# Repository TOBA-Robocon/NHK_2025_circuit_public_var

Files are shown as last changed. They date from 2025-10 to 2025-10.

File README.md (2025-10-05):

# 前提(注意)
USB-CのD+,D-にCANを流す異端ゲキヤバ思想。
USBに規格外信号を流すなって人はブラウザバックを推奨。
著作権保護とかのために本番で使ったデータをちょっと改変してたりする。

# 各基板説明

## CAN_HUB_SMD
USB-CのCANバスを分岐するための基板。

付属のXT60に給電することで分岐先のUSB-Cの電源ラインに電源を供給できる。

電源を供給することで後述する「偽C610(C810)」を駆動させることができる。

本番で使った基板にはれな子のシルクが乗っているため、部内では「れな子」と呼ばれていた。

## CANはぶ
CAN_HUB_SMDの旧バージョン。

使ってるUSB-Cのコネクタが違う。

## GOD_DC_MD
強いモタドラ

定格:40V/60A

## Next_main_Control
メインの基板。

ESP32とF405RGTがついている。Dualshock4の値をESP32で受け取ってCANバスに流し散らかす。

Dualshock4の値を使って各機構の処理をし、4本のUSB-C_CANで各基板にデータを転送する。

ESP32で流すデータの種類とか規格は「ESP32」フォルダの中を参照のこと。

## mecanum_HUB
メカナムを動かしている基板

CAN*1、ロリコン*2(XAコネクタ5pin)、リミットスイッチ*2(XAコネクタ2pin)、電流センサ*2、「GOD_DC_MD」を刺すスロット*2,

メイン基板からのデューティー比と回転方向司令をCANで受けてメカナムを回す

## ガチ夫
ベル直道機構をPID制御する基板

定格:40V/20A

CAN*1、ロリコン*1(XAコネクタ5pin)、リミットスイッチ*1(PHコネクタ2pin)、電流センサ*1、モータードライバ*1ch

メイン基板から速度司令をCANで受けて定速度でベル直を回す。

## 偽C610(C810)
C610サイズのDCモータードライバ

定格:24V/5A

USB-Cから電源とCANを引ける

CAN*1、リミットスイッチ*1(PHコネクタ2pin)、モータードライバ*1ch

メイン基板からデューティー比と回転方向司令をCANで受けてモーターを回す。

基板をロボットに固定するのがめんどくさすぎる駄作。

# iocs
各基板に乗っているSTM32用の.iocファイル群

参考程度にCubeIDE等で使って、どうぞ。

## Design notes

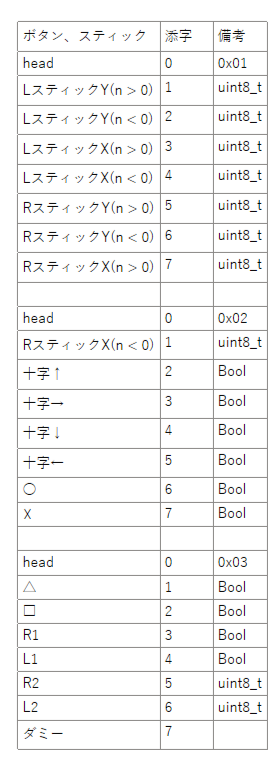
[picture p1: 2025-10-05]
ESP32/スクリーンショット 2025-10-06 024648.png

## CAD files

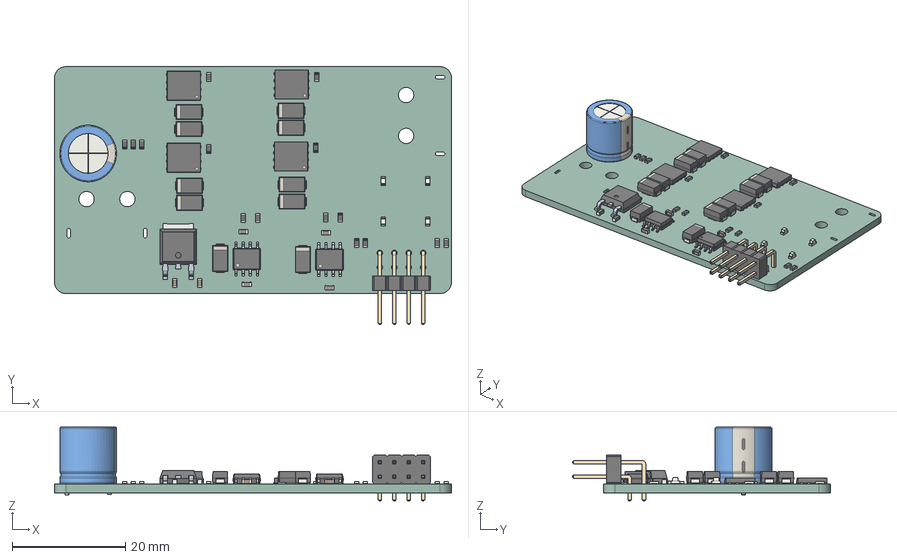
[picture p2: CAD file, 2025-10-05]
GOD_DC_MD/GOD_DC_MD.step
70.0 x 45.4 x 13.0 mm
CP_Radial_D100mm_P750mm
D_SMA x 10
SOIC_8_39x49mm_P127mm x 2
PinHeader_2x04_P254mm_Horizontal
C_0603_1608Metric x 6
R_0603_1608Metric x 15
TDSON_8_1 x 4
LED_0603_1608Metric x 4
CQ assembly
GOD_DC_MD_PCB

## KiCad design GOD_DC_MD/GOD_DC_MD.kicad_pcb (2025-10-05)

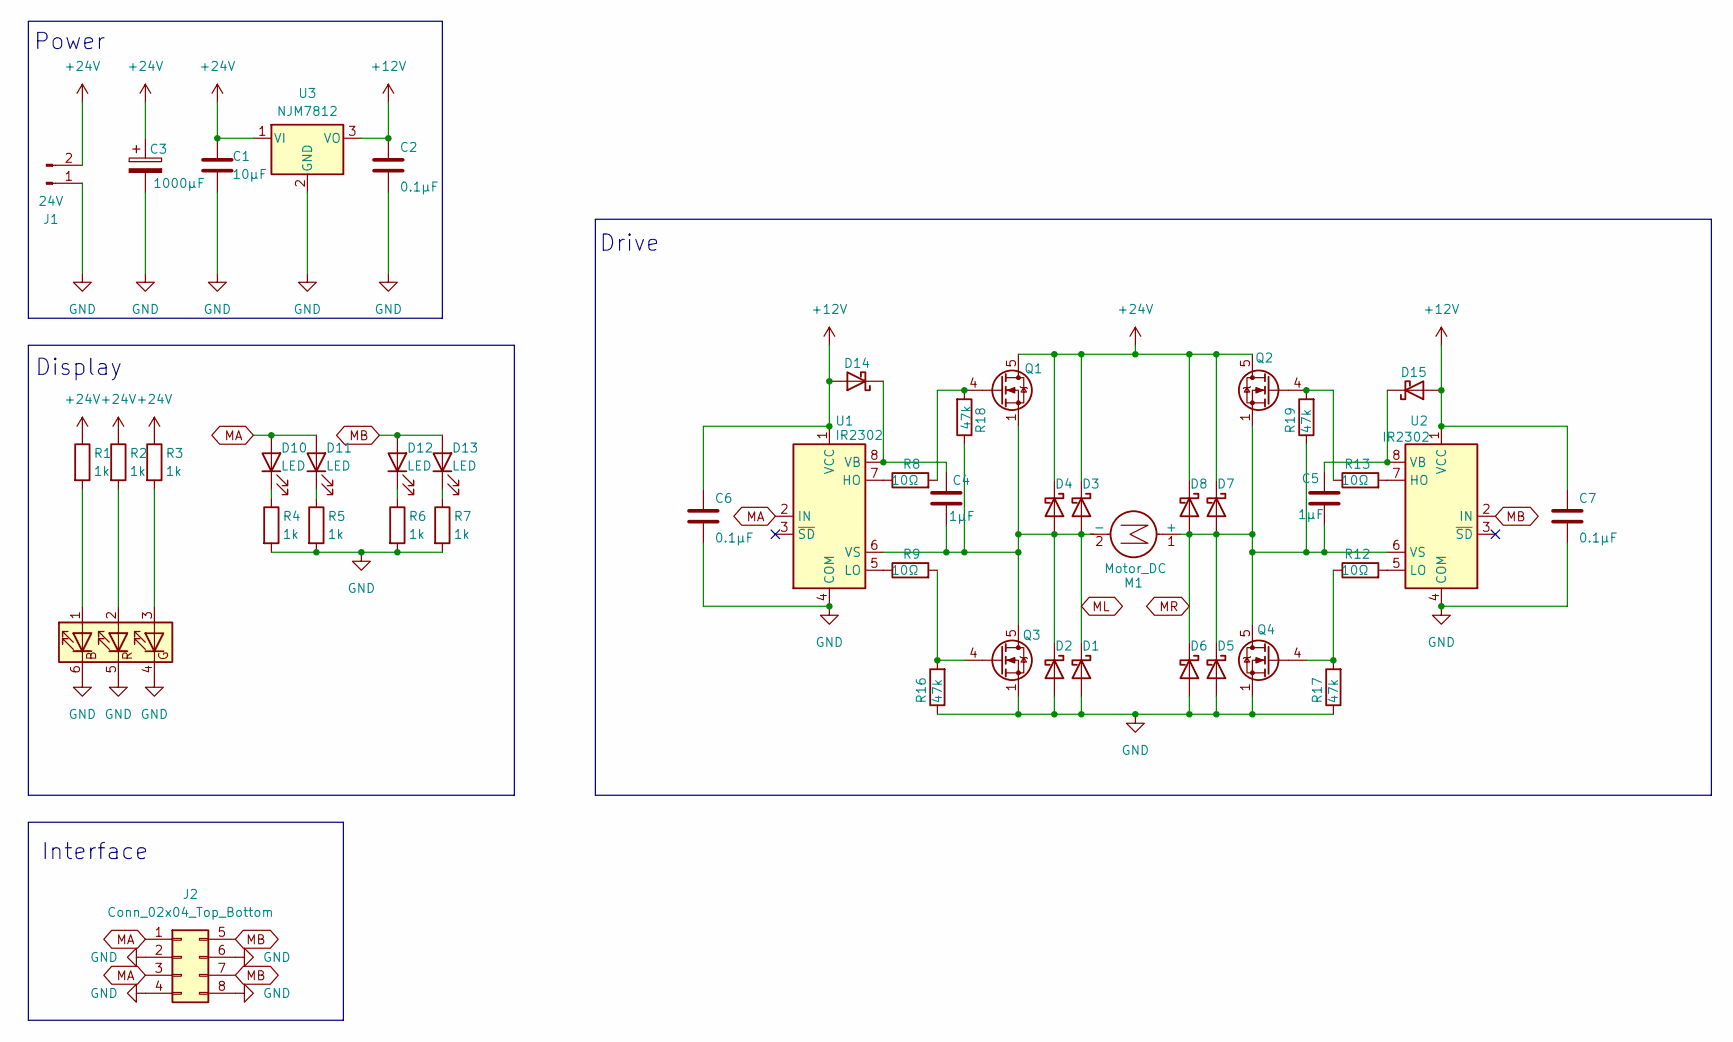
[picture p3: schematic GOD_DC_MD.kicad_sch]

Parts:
C1: 10μF; C_0603_1608Metric_Pad1.08x0.95mm_HandSolder
C2, C6, C7: 0.1μF; C_0603_1608Metric_Pad1.08x0.95mm_HandSolder
C3: 1000μF; CP_Radial_D10.0mm_P7.50mm
C4, C5: 1μF; C_0603_1608Metric_Pad1.08x0.95mm_HandSolder
D1, D2, D3, D4, D5, D6, D7, D8, D14, D15: SS14; D_SMA_Handsoldering
D9: SMLVN6RGB; LED_ROHM_SMLVN6
D10, D11, D12, D13: LED; LED_0603_1608Metric_Pad1.05x0.95mm_HandSolder
J1: 24V; AMASS_XT60PW-M_1x02_P7.20mm_Horizontal
J2: Conn_02x04_Top_Bottom; PinHeader_2x04_P2.54mm_Horizontal
M1: Motor_DC; AMASS_XT60PW-F_1x02_P7.20mm_Horizontal
Q1, Q2, Q3, Q4: BSC159N10LSFG; TDSON-8-1
R1, R2, R3, R4, R5, R6, R7: 1k; R_0603_1608Metric_Pad0.98x0.95mm_HandSolder
R8, R9, R12, R13: 10Ω; R_0603_1608Metric_Pad0.98x0.95mm_HandSolder
R16, R17, R18, R19: 47k; R_0603_1608Metric_Pad0.98x0.95mm_HandSolder
U1, U2: IR2302; SOIC-8_3.9x4.9mm_P1.27mm
U3: NJM7812; TO-252-2

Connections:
+12V: C2.1, C6.1, C7.1, D14.2 (A), D15.2 (A), U1.1 (VCC), U2.1 (VCC), U3.3 (VO)
+24V: C1.1, C3.1, D3.1 (K), D4.1 (K), D7.1 (K), D8.1 (K), J1.2, Q1.5 (D), Q2.5 (D), R1.1, R2.1, R3.1, U3.1 (VI)
GND: C1.2, C2.2, C3.2, C6.2, C7.2, D1.2 (A), D2.2 (A), D5.2 (A), D6.2 (A), D9.4 (GK), D9.5 (RK), D9.6 (BK), J1.1, J2.2, J2.4, J2.6, J2.8, Q3.1 (S), Q3.2 (S), Q3.3 (S), Q4.1 (S), Q4.2 (S), Q4.3 (S), R4.2, R5.2, R6.2, R7.2, R16.1, R17.1, U1.4 (COM), U2.4 (COM), U3.2 (GND)
MA: D10.2 (A), D11.2 (A), J2.1, J2.3, U1.2 (IN)
MB: D12.2 (A), D13.2 (A), J2.5, J2.7, U2.2 (IN)
ML: C4.2, D1.1 (K), D2.1 (K), D3.2 (A), D4.2 (A), M1.2 (-), Q1.1 (S), Q1.2 (S), Q1.3 (S), Q3.5 (D), R18.1, U1.6 (VS)
MR: C5.2, D5.1 (K), D6.1 (K), D7.2 (A), D8.2 (A), M1.1 (+), Q2.1 (S), Q2.2 (S), Q2.3 (S), Q4.5 (D), R19.1, U2.6 (VS)
unnamed: D9.1 (BA), R1.2
unnamed: D9.3 (GA), R3.2
unnamed: D9.2 (RA), R2.2
unnamed: D10.1 (K), R4.1
unnamed: D11.1 (K), R5.1
unnamed: D12.1 (K), R6.1
unnamed: D13.1 (K), R7.1
unnamed: C4.1, D14.1 (K), U1.8 (VB)
unnamed: C5.1, D15.1 (K), U2.8 (VB)
unnamed: Q1.4 (G), R8.2, R18.2
unnamed: Q2.4 (G), R13.1, R19.2
unnamed: Q3.4 (G), R9.2, R16.2
unnamed: Q4.4 (G), R12.1, R17.2
unnamed: R8.1, U1.7 (HO)
unnamed: R9.1, U1.5 (LO)
unnamed: R13.2, U2.7 (HO)
unnamed: R12.2, U2.5 (LO)

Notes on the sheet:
Display
Drive
Interface
Power

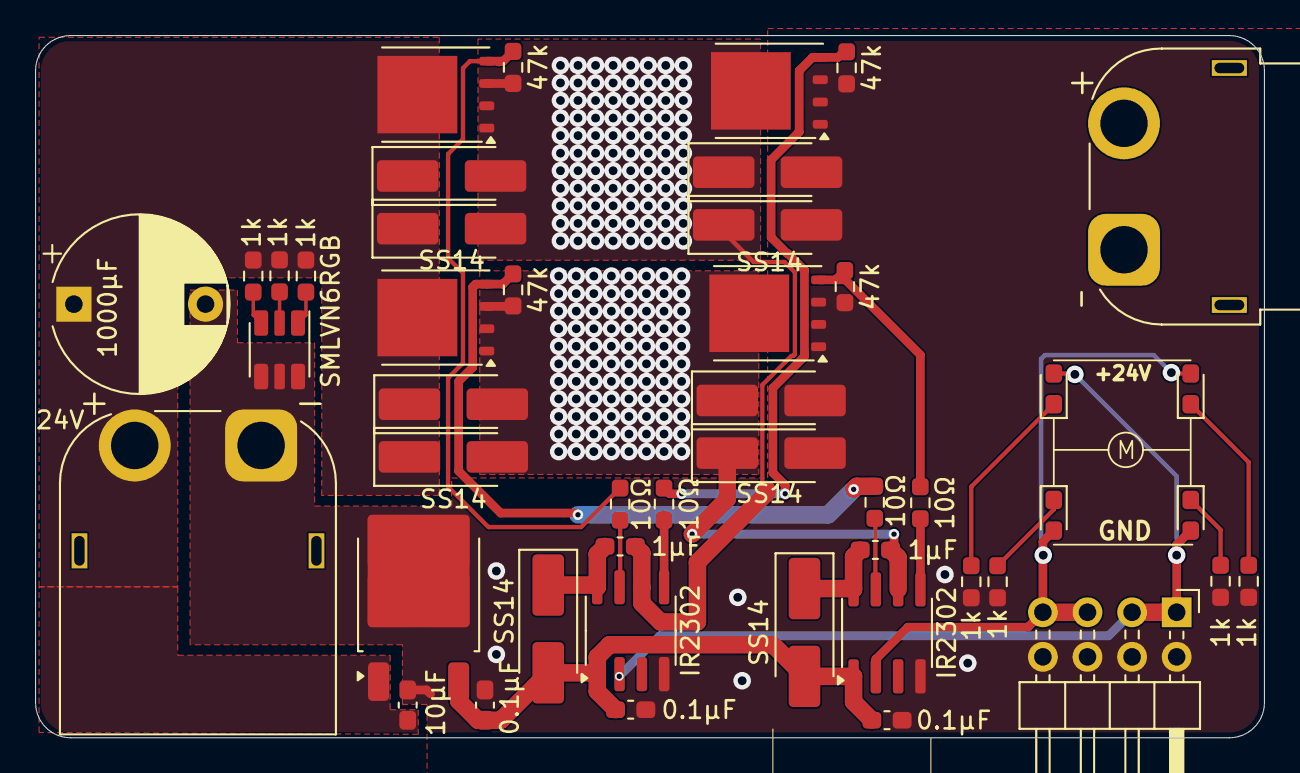
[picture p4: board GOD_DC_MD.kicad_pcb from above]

Board: 2 copper layers, 70.0 x 40.0 mm, 47 parts (0 on the bottom side), 24 nets.

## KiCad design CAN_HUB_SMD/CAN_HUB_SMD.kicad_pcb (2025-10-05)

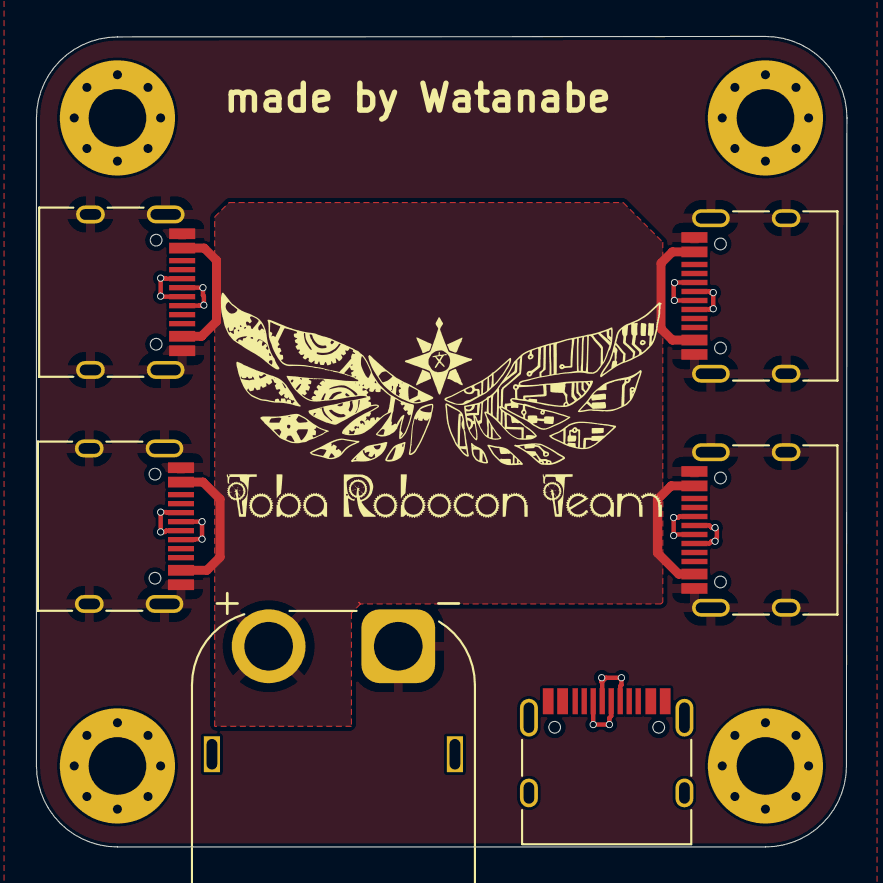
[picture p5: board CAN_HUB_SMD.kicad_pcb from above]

Board: 2 copper layers, 45.0 x 45.0 mm, 10 parts (0 on the bottom side), 5 nets.

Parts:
H1, H2, H3, H4: MountingHole_Pad; MountingHole_3.2mm_M3_Pad_Via
J1: Conn_01x02_Pin; AMASS_XT60PW-M_1x02_P7.20mm_Horizontal
J2, J3, J4, J5, J6: USB_C_Receptacle_USB2.0_16P; USB_C_Receptacle_HRO_TYPE-C-31-M-12

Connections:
+24V: J1.2, J3.A4 (VBUS), J3.A9 (VBUS), J3.B4 (VBUS), J3.B9 (VBUS), J4.A4 (VBUS), J4.A9 (VBUS), J4.B4 (VBUS), J4.B9 (VBUS), J5.A4 (VBUS), J5.A9 (VBUS), J5.B4 (VBUS), J5.B9 (VBUS), J6.A4 (VBUS), J6.A9 (VBUS), J6.B4 (VBUS), J6.B9 (VBUS)
CAN_H: J2.A6 (D+), J2.B6 (D+), J3.A6 (D+), J3.B6 (D+), J4.A6 (D+), J4.B6 (D+), J5.A6 (D+), J5.B6 (D+), J6.A6 (D+), J6.B6 (D+)
CAN_L: J2.A7 (D-), J2.B7 (D-), J3.A7 (D-), J3.B7 (D-), J4.A7 (D-), J4.B7 (D-), J5.A7 (D-), J5.B7 (D-), J6.A7 (D-), J6.B7 (D-)
GND: J1.1, J3.A1 (GND), J3.A12 (GND), J3.B1 (GND), J3.B12 (GND), J3.S1 (SHIELD), J4.A1 (GND), J4.A12 (GND), J4.B1 (GND), J4.B12 (GND), J4.S1 (SHIELD), J5.A1 (GND), J5.A12 (GND), J5.B1 (GND), J5.B12 (GND), J5.S1 (SHIELD), J6.A1 (GND), J6.A12 (GND), J6.B1 (GND), J6.B12 (GND), J6.S1 (SHIELD)
unnamed: J2.A1 (GND), J2.A12 (GND), J2.B1 (GND), J2.B12 (GND)

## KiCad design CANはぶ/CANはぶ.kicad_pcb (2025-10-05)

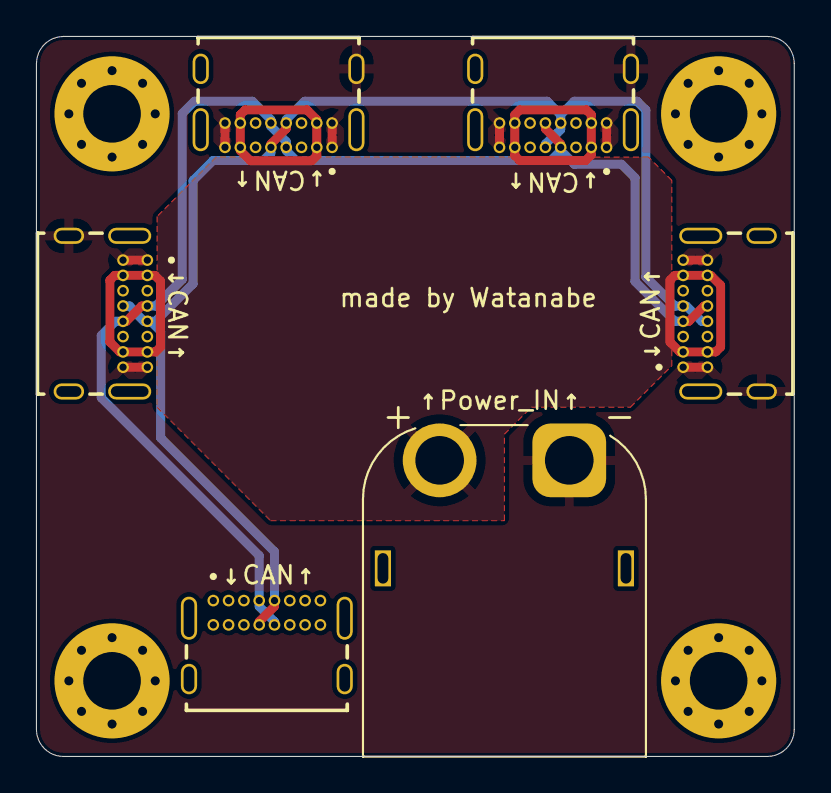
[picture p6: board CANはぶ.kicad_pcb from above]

Board: 2 copper layers, 42.1 x 40.0 mm, 10 parts (0 on the bottom side), 4 nets.

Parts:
H1, H2, H3, H4: MountingHole_Pad; MountingHole_3.2mm_M3_Pad_Via
J1, J2, J3, J4, J5: USB_C_Receptacle_USB2.0_16P; GCT_USB4085-GF-A_REVB
J6: Conn_01x02_Pin; AMASS_XT60PW-M_1x02_P7.20mm_Horizontal

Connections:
+24V: J1.A4 (VBUS), J1.A9 (VBUS), J1.B4 (VBUS), J1.B9 (VBUS), J2.A4 (VBUS), J2.A9 (VBUS), J2.B4 (VBUS), J2.B9 (VBUS), J3.A4 (VBUS), J3.A9 (VBUS), J3.B4 (VBUS), J3.B9 (VBUS), J4.A4 (VBUS), J4.A9 (VBUS), J4.B4 (VBUS), J4.B9 (VBUS), J6.2
CAN_H: J1.A7 (D-), J1.B7 (D-), J2.A7 (D-), J2.B7 (D-), J3.A7 (D-), J3.B7 (D-), J4.A7 (D-), J4.B7 (D-), J5.A7 (D-), J5.B7 (D-)
CAN_L: J1.A6 (D+), J1.B6 (D+), J2.A6 (D+), J2.B6 (D+), J3.A6 (D+), J3.B6 (D+), J4.A6 (D+), J4.B6 (D+), J5.A6 (D+), J5.B6 (D+)
GND: J1.A1 (GND), J1.A12 (GND), J1.B1 (GND), J1.B12 (GND), J1.S1 (SHIELD), J2.A1 (GND), J2.A12 (GND), J2.B1 (GND), J2.B12 (GND), J2.S1 (SHIELD), J3.A1 (GND), J3.A12 (GND), J3.B1 (GND), J3.B12 (GND), J3.S1 (SHIELD), J4.A1 (GND), J4.A12 (GND), J4.B1 (GND), J4.B12 (GND), J4.S1 (SHIELD), J6.1

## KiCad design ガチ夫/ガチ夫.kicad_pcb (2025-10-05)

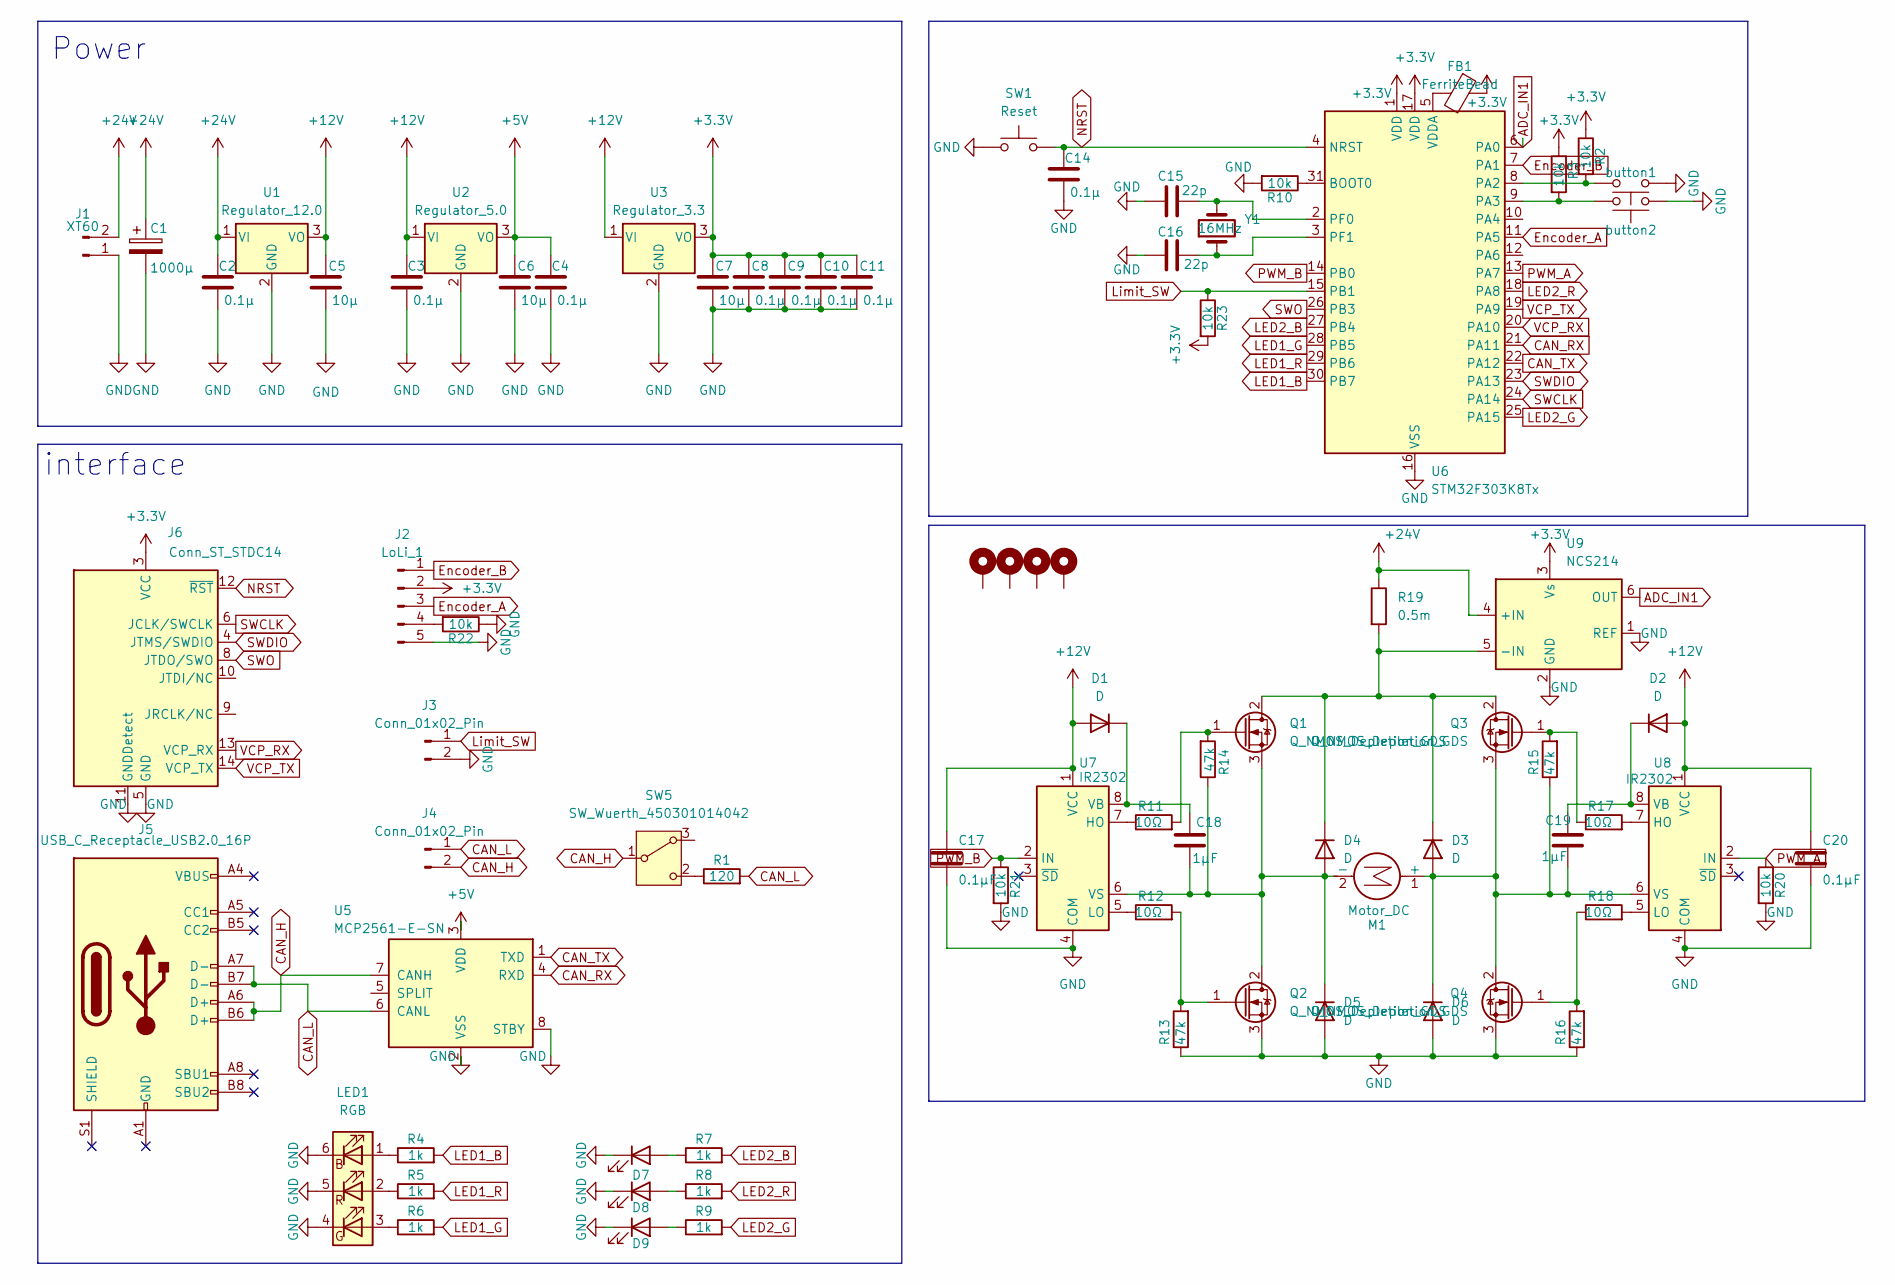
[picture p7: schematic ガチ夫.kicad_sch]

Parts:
C1: 1000μ; CP_Radial_D12.5mm_P5.00mm
C2, C3, C4, C8, C9, C10, C11, C14: 0.1μ; C_0603_1608Metric
C5, C6, C7: 10μ; C_0603_1608Metric
C15, C16: 22p; C_0603_1608Metric
C17, C20: 0.1μF; C_0603_1608Metric_Pad1.08x0.95mm_HandSolder
C18, C19: 1μF; C_0603_1608Metric_Pad1.08x0.95mm_HandSolder
D1, D2, D3, D4, D5, D6: D; D_SOD-123F
D7, D8, D9: LED; LED_0603_1608Metric
FB1: FerriteBead; L_0805_2012Metric_Pad1.05x1.20mm_HandSolder
H1, H2, H3, H4: MountingHole_Pad; MountingHole_3.2mm_M3_Pad_Via
J1: XT60; AMASS_XT60PW-M_1x02_P7.20mm_Horizontal
J2: LoLi_1; JST_XA_B05B-XASK-1_1x05_P2.50mm_Vertical
J3: Conn_01x02_Pin; JST_PH_B2B-PH-SM4-TB_1x02-1MP_P2.00mm_Vertical
J4: Conn_01x02_Pin; JST_XA_S02B-XASK-1N-BN_1x02_P2.50mm_Horizontal
J5: USB_C_Receptacle_USB2.0_16P; GCT_USB4085-GF-A_REVB
J6: Conn_ST_STDC14; PinHeader_2x07_P1.27mm_Vertical
LED1: RGB; LED_ROHM_SMLVN6
M1: Motor_DC; AMASS_XT60PW-F_1x02_P7.20mm_Horizontal
Q1, Q2, Q3, Q4: Q_NMOS_Depletion_GDS; TO-252-2
R1: 120; R_0603_1608Metric_Pad0.98x0.95mm_HandSolder
R2, R3, R10, R20, R21, R22, R23: 10k; R_0603_1608Metric
R4, R5, R6, R7, R8, R9: 1k; R_0603_1608Metric_Pad0.98x0.95mm_HandSolder
R11, R12, R17, R18: 10Ω; R_0603_1608Metric_Pad0.98x0.95mm_HandSolder
R13, R14, R15, R16: 47k; R_0603_1608Metric_Pad0.98x0.95mm_HandSolder
R19: 0.5m; R_2512_6332Metric
SW1: Reset; SW_PUSH_1P1T_6x3.5mm_H5.0_APEM_MJTP1250
SW3: button2; SW_PUSH_1P1T_6x3.5mm_H5.0_APEM_MJTP1250
SW4: button1; SW_PUSH_1P1T_6x3.5mm_H5.0_APEM_MJTP1250
SW5: SW_Wuerth_450301014042; SW_Slide-03_Wuerth-WS-SLTV_10x2.5x6.4_P2.54mm
U1: Regulator_12.0; TO-252-2
U2: Regulator_5.0; TO-252-2
U3: Regulator_3.3; TO-252-2
U5: MCP2561-E-SN; SOIC-8_3.9x4.9mm_P1.27mm
U6: STM32F303K8Tx; LQFP-32_7x7mm_P0.8mm
U7, U8: IR2302; SOIC-8_3.9x4.9mm_P1.27mm
U9: NCS214; SOT-363_SC-70-6_Handsoldering
Y1: 16MHz; Crystal_HC18-U_Vertical

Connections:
+3.3V: C7.1, C8.1, C9.1, C10.1, C11.1, FB1.1, J2.2, J6.3 (VCC), R2.1, R3.1, R23.2, U3.3 (VO), U6.1 (VDD), U6.17 (VDD), U9.3 (Vs)
+5V: C4.1, C6.1, U2.3 (VO), U5.3 (VDD)
+12V: C3.1, C5.1, C17.1, C20.1, D1.2 (A), D2.2 (A), U1.3 (VO), U2.1 (VI), U3.1 (VI), U7.1 (VCC), U8.1 (VCC)
+24V: C1.1, C2.1, J1.2, R19.1, U1.1 (VI), U9.4 (+IN)
ADC_IN1: U6.6 (PA0), U9.6 (OUT)
CAN_H: J4.2, J5.A6 (D+), J5.B6 (D+), SW5.1 (B), U5.7 (CANH)
CAN_L: J4.1, J5.A7 (D-), J5.B7 (D-), R1.2, U5.6 (CANL)
CAN_RX: U5.4 (RXD), U6.21 (PA11)
CAN_TX: U5.1 (TXD), U6.22 (PA12)
Encoder_A: J2.3, U6.11 (PA5)
Encoder_B: J2.1, U6.7 (PA1)
GND: C1.2, C2.2, C3.2, C4.2, C5.2, C6.2, C7.2, C8.2, C9.2, C10.2, C11.2, C14.2, C15.1, C16.1, C17.2, C20.2, D5.2 (A), D6.2 (A), D7.1 (K), D8.1 (K), D9.1 (K), J1.1, J2.5, J3.2, J6.5 (GND), J6.7 (GND), J6.11 (GNDDetect), LED1.4 (GK), LED1.5 (RK), LED1.6 (BK), Q2.3 (S), Q4.3 (S), R10.2, R13.1, R16.1, R20.2, R21.2, R22.1, SW1.1, SW3.1, SW4.1, U1.2 (GND), U2.2 (GND), U3.2 (GND), U5.2 (VSS), U5.8 (STBY), U6.16 (VSS), U6.32 (VSS), U7.4 (COM), U8.4 (COM), U9.1 (REF), U9.2 (GND)
LED1_B: R4.2, U6.30 (PB7)
LED1_G: R6.2, U6.28 (PB5)
LED1_R: R5.2, U6.29 (PB6)
LED2_B: R7.2, U6.27 (PB4)
LED2_G: R9.2, U6.25 (PA15)
LED2_R: R8.2, U6.18 (PA8)
Limit_SW: J3.1, R23.1, U6.15 (PB1)
NRST: C14.1, J6.12 (~RST), SW1.2, U6.4 (NRST)
unnamed: C18.1, D1.1 (K), U7.8 (VB)
unnamed: C19.1, D2.1 (K), U8.8 (VB)
unnamed: C19.2, D3.2 (A), D6.1 (K), M1.1 (+), Q3.3 (S), Q4.2 (D), R15.1, U8.6 (VS)
unnamed: D3.1 (K), D4.1 (K), Q1.2 (D), Q3.2 (D), R19.2, U9.5 (-IN)
unnamed: C18.2, D4.2 (A), D5.1 (K), M1.2 (-), Q1.3 (S), Q2.2 (D), R14.1, U7.6 (VS)
unnamed: D7.2 (A), R7.1
unnamed: D8.2 (A), R8.1
unnamed: D9.2 (A), R9.1
unnamed: J2.4, R22.2
unnamed: LED1.1 (BA), R4.1
unnamed: LED1.3 (GA), R6.1
unnamed: LED1.2 (RA), R5.1
unnamed: Q1.1 (G), R11.2, R14.2
unnamed: Q2.1 (G), R12.2, R13.2
unnamed: Q3.1 (G), R15.2, R17.1
unnamed: Q4.1 (G), R16.2, R18.1
unnamed: R1.1, SW5.2 (C)
unnamed: R10.1, U6.31 (BOOT0)
unnamed: R2.2, SW4.2, U6.8 (PA2)
unnamed: R3.2, SW3.2, U6.9 (PA3)
unnamed: C15.2, U6.2 (PF0), Y1.2
unnamed: C16.2, U6.3 (PF1), Y1.1
unnamed: FB1.2, U6.5 (VDDA)
unnamed: R11.1, U7.7 (HO)
unnamed: R12.1, U7.5 (LO)
unnamed: R17.2, U8.7 (HO)
unnamed: R18.2, U8.5 (LO)
PWM_A: R20.1, U6.13 (PA7), U8.2 (IN)
PWM_B: R21.1, U6.14 (PB0), U7.2 (IN)
SWCLK: J6.6 (JCLK/SWCLK), U6.24 (PA14)
SWDIO: J6.4 (JTMS/SWDIO), U6.23 (PA13)
SWO: J6.8 (JTDO/SWO), U6.26 (PB3)
VCP_RX: J6.13 (VCP_RX), U6.20 (PA10)
VCP_TX: J6.14 (VCP_TX), U6.19 (PA9)

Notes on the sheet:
interface
Power

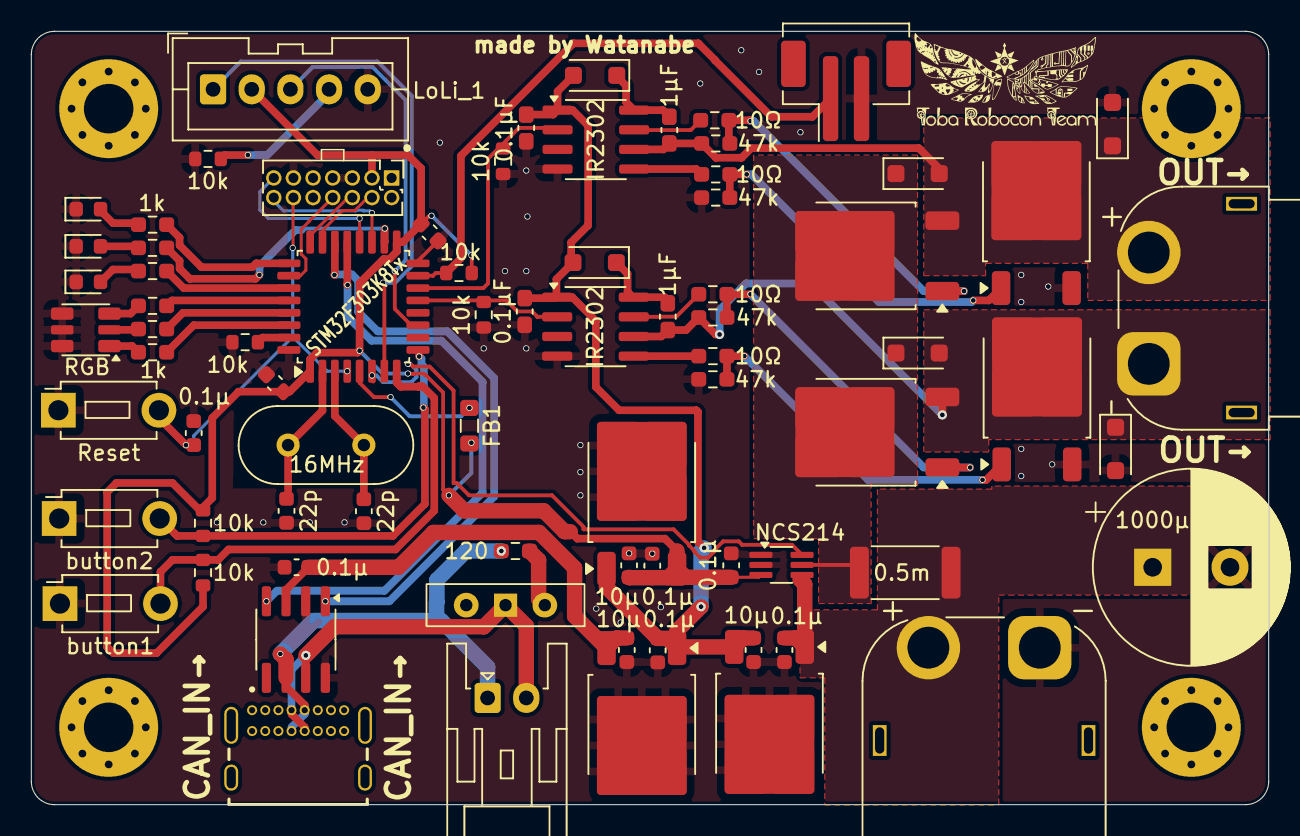
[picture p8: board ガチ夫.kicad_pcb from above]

Board: 2 copper layers, 80.0 x 50.0 mm, 80 parts (0 on the bottom side), 54 nets.

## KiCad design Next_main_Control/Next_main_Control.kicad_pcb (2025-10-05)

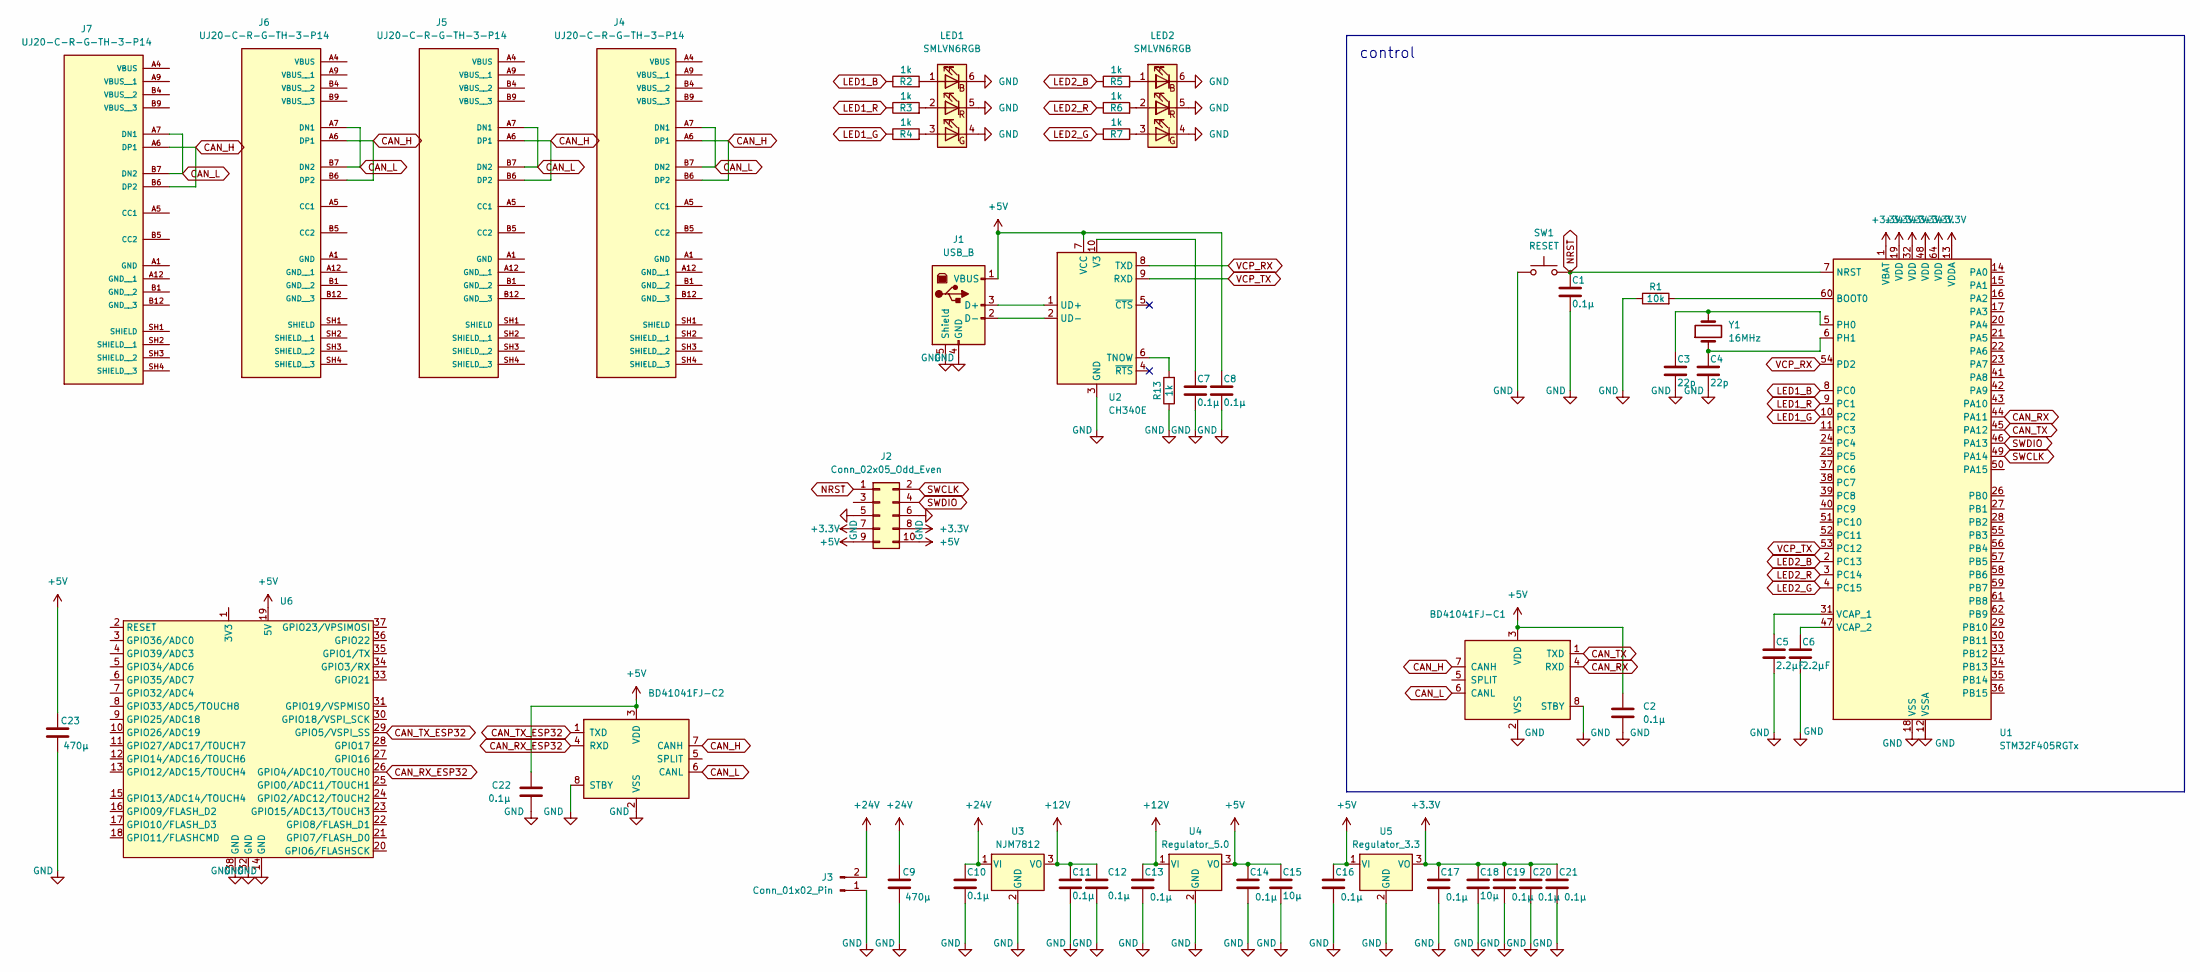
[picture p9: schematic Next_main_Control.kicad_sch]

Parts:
BD41041FJ-C1, BD41041FJ-C2: MCP2561-E-SN; SOIC-8_3.9x4.9mm_P1.27mm
C1, C2, C7, C8, C10, C11, C12, C13, C14, C16, C17, C19, C20, C21, C22: 0.1μ; C_0603_1608Metric_Pad1.08x0.95mm_HandSolder
C3, C4: 22p; C_0603_1608Metric_Pad1.08x0.95mm_HandSolder
C5, C6: 2.2μF; C_0603_1608Metric_Pad1.08x0.95mm_HandSolder
C9, C23: 470μ; CP_Radial_D8.0mm_P5.00mm
C15, C18: 10μ; C_0603_1608Metric_Pad1.08x0.95mm_HandSolder
J1: USB_B; USB_B_OST_USB-B1HSxx_Horizontal
J2: Conn_02x05_Odd_Even; IDC-Header_2x05_P2.54mm_Vertical
J3: Conn_01x02_Pin; AMASS_XT60PW-M_1x02_P7.20mm_Horizontal
J4, J5, J6, J7: UJ20-C-R-G-TH-3-P14; SAMESKY_UJ20-C-R-G-TH-3-P14; PARTREV 1.0
LED1, LED2: SMLVN6RGB; LED_ROHM_SMLVN6
R1: 10k; R_0603_1608Metric_Pad0.98x0.95mm_HandSolder
R2, R3, R4, R5, R6, R7, R13: 1k; R_0603_1608Metric_Pad0.98x0.95mm_HandSolder
SW1: RESET; SW_PUSH_6mm
U1: STM32F405RGTx; LQFP-64_10x10mm_P0.5mm
U2: CH340E; MSOP-10_3x3mm_P0.5mm
U3: NJM7812; TO-252-2
U4: Regulator_5.0; TO-252-2
U5: Regulator_3.3; TO-252-2
U6: ESP32_DevkitC
Y1: 16MHz; Crystal_HC18-U_Vertical

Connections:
+3.3V: C17.1, C18.1, C19.1, C20.1, C21.1, J2.7, J2.8, U1.1 (VBAT), U1.13 (VDDA), U1.19 (VDD), U1.32 (VDD), U1.48 (VDD), U1.64 (VDD), U5.3 (VO)
+5V: BD41041FJ-C1.3 (VDD), BD41041FJ-C2.3 (VDD), C2.1, C8.1, C14.1, C15.1, C16.1, C22.1, C23.1, J1.1 (VBUS), J2.9, J2.10, U2.7 (VCC), U4.3 (VO), U5.1 (VI), U6.19 (5V)
+12V: C11.1, C12.1, C13.1, U3.3 (VO), U4.1 (VI)
+24V: C9.1, C10.1, J3.2, U3.1 (VI)
CAN_H: BD41041FJ-C1.7 (CANH), BD41041FJ-C2.7 (CANH), J4.A6 (DP1), J4.B6 (DP2), J5.A6 (DP1), J5.B6 (DP2), J6.A6 (DP1), J6.B6 (DP2), J7.A6 (DP1), J7.B6 (DP2)
CAN_L: BD41041FJ-C1.6 (CANL), BD41041FJ-C2.6 (CANL), J4.A7 (DN1), J4.B7 (DN2), J5.A7 (DN1), J5.B7 (DN2), J6.A7 (DN1), J6.B7 (DN2), J7.A7 (DN1), J7.B7 (DN2)
CAN_RX: BD41041FJ-C1.4 (RXD), U1.44 (PA11)
CAN_RX_ESP32: BD41041FJ-C2.4 (RXD), U6.26 (GPIO4/ADC10/TOUCH0)
CAN_TX: BD41041FJ-C1.1 (TXD), U1.45 (PA12)
CAN_TX_ESP32: BD41041FJ-C2.1 (TXD), U6.29 (GPIO5/VSPI_SS)
GND: BD41041FJ-C1.2 (VSS), BD41041FJ-C1.8 (STBY), BD41041FJ-C2.2 (VSS), BD41041FJ-C2.8 (STBY), C1.2, C2.2, C3.2, C4.2, C5.2, C6.2, C7.2, C8.2, C9.2, C10.2, C11.2, C12.2, C13.2, C14.2, C15.2, C16.2, C17.2, C18.2, C19.2, C20.2, C21.2, C22.2, C23.2, J1.4 (GND), J1.5 (Shield), J2.5, J2.6, J3.1, LED1.4 (GK), LED1.5 (RK), LED1.6 (BK), LED2.4 (GK), LED2.5 (RK), LED2.6 (BK), R1.1, R13.1, SW1.1, U1.12 (VSSA), U1.18 (VSS), U1.63 (VSS), U2.3 (GND), U3.2 (GND), U4.2 (GND), U5.2 (GND), U6.14 (GND), U6.32 (GND), U6.38 (GND)
LED1_B: R2.1, U1.8 (PC0)
LED1_G: R4.1, U1.10 (PC2)
LED1_R: R3.1, U1.9 (PC1)
LED2_B: R5.1, U1.2 (PC13)
LED2_G: R7.1, U1.4 (PC15)
LED2_R: R6.1, U1.3 (PC14)
NRST: C1.1, J2.1, SW1.2, U1.7 (NRST)
unnamed: J1.3 (D+), U2.1 (UD+)
unnamed: J1.2 (D-), U2.2 (UD-)
unnamed: LED1.1 (BA), R2.2
unnamed: LED1.3 (GA), R4.2
unnamed: LED1.2 (RA), R3.2
unnamed: LED2.1 (BA), R5.2
unnamed: LED2.3 (GA), R7.2
unnamed: LED2.2 (RA), R6.2
unnamed: R1.2, U1.60 (BOOT0)
unnamed: C3.1, U1.5 (PH0), Y1.2
unnamed: C4.1, U1.6 (PH1), Y1.1
unnamed: C5.1, U1.31 (VCAP_1)
unnamed: C6.1, U1.47 (VCAP_2)
unnamed: R13.2, U2.6 (TNOW)
unnamed: C7.1, U2.10 (V3)
SWCLK: J2.2, U1.49 (PA14)
SWDIO: J2.4, U1.46 (PA13)
VCP_RX: U1.54 (PD2), U2.8 (TXD)
VCP_TX: U1.53 (PC12), U2.9 (RXD)

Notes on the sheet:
control

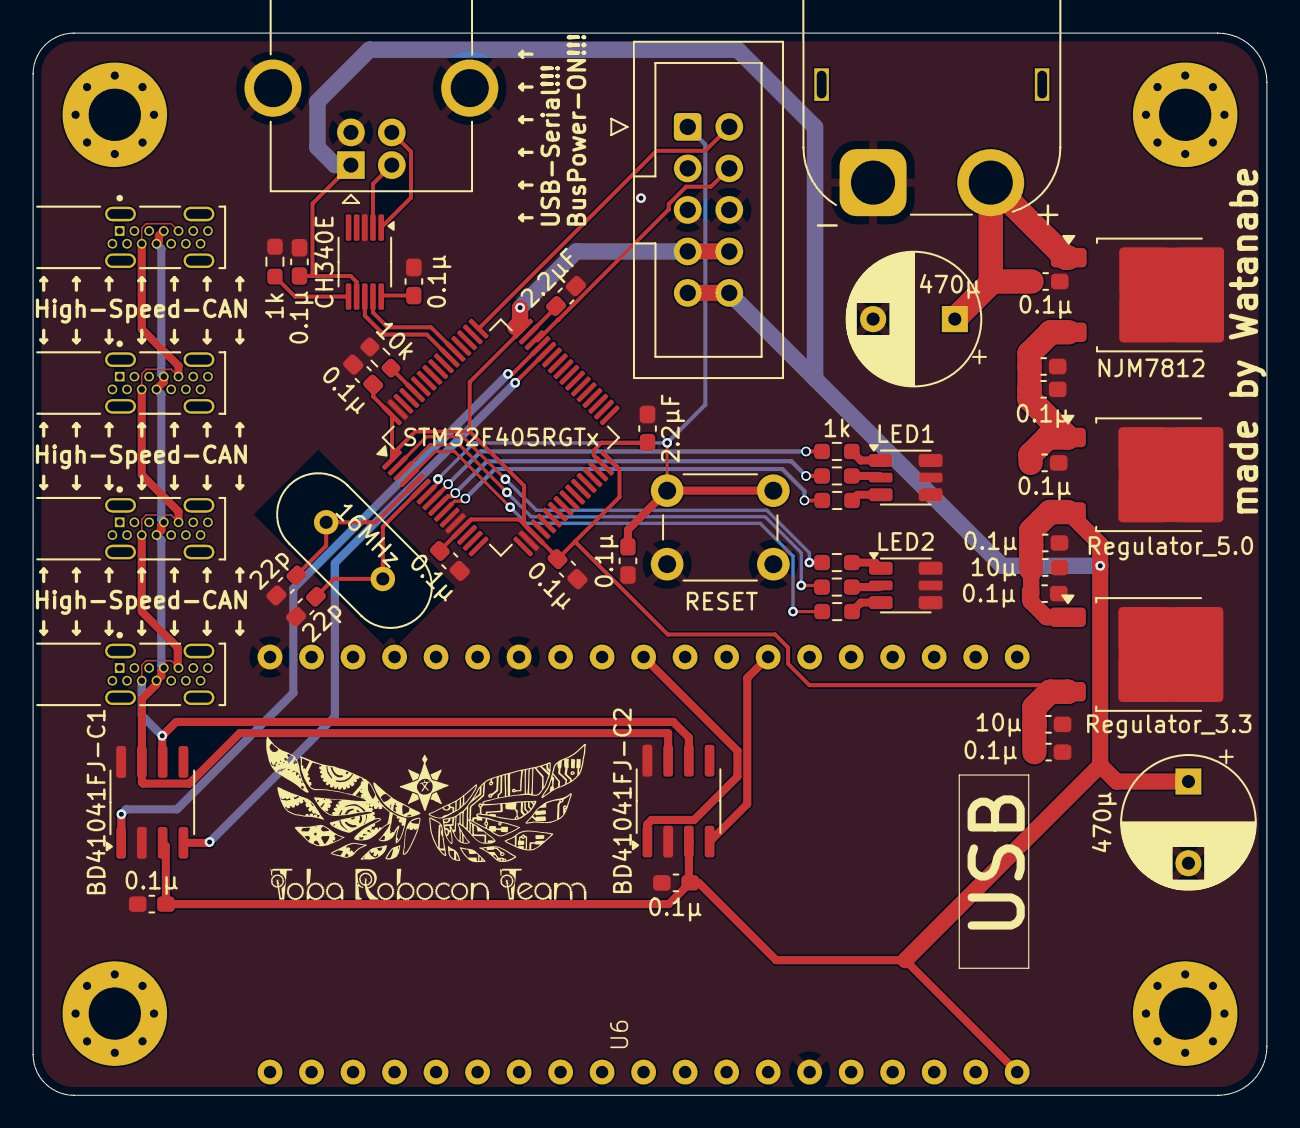
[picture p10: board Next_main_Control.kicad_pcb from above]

Board: 2 copper layers, 75.5 x 65.0 mm, 50 parts (0 on the bottom side), 37 nets.

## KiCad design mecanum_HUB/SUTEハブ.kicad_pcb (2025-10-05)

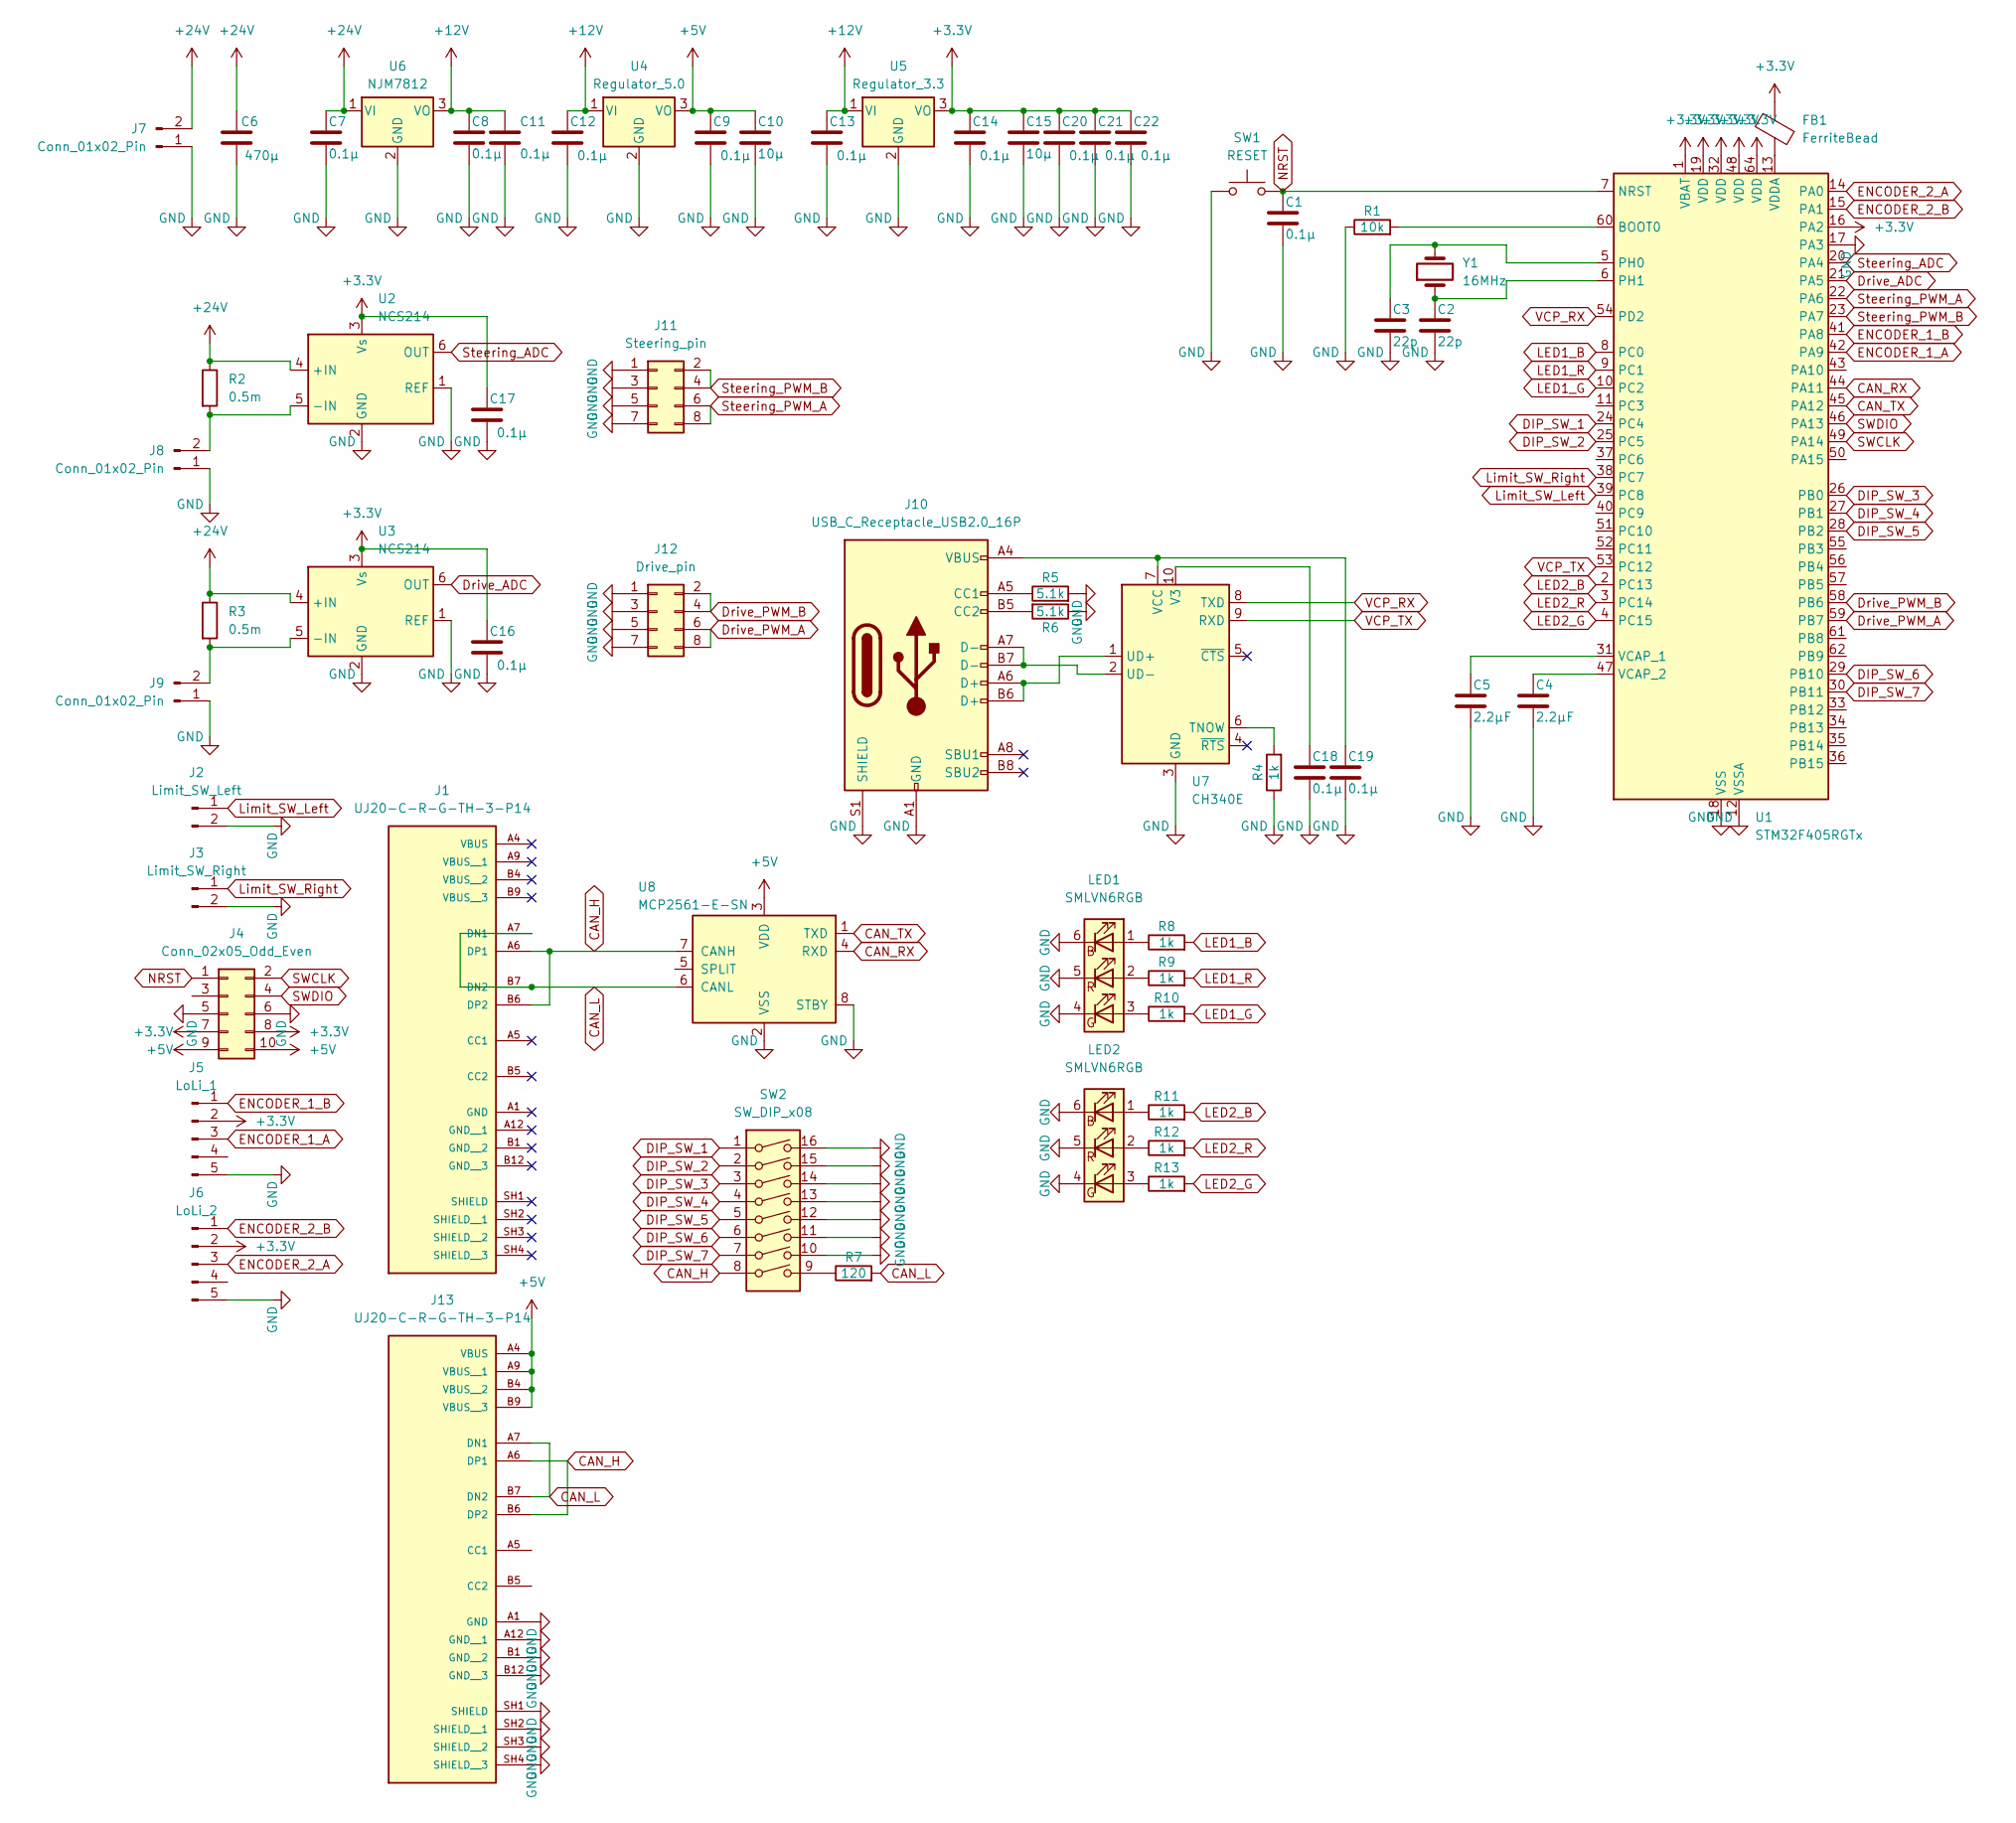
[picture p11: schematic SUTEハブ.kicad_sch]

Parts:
C1, C7, C8, C9, C11, C12, C13, C14, C16, C17, C18, C19, C20, C21, C22: 0.1μ; C_0603_1608Metric_Pad1.08x0.95mm_HandSolder
C2, C3: 22p; C_0603_1608Metric_Pad1.08x0.95mm_HandSolder
C4, C5: 2.2μF; C_0603_1608Metric_Pad1.08x0.95mm_HandSolder
C6: 470μ; CP_Radial_D8.0mm_P5.00mm
C10, C15: 10μ; C_0603_1608Metric_Pad1.08x0.95mm_HandSolder
FB1: FerriteBead; L_0805_2012Metric_Pad1.05x1.20mm_HandSolder
J1, J13: UJ20-C-R-G-TH-3-P14; SAMESKY_UJ20-C-R-G-TH-3-P14; PARTREV 1.0
J2: Limit_SW_Left; JST_XA_B02B-XASK-1_1x02_P2.50mm_Vertical
J3: Limit_SW_Right; JST_XA_B02B-XASK-1_1x02_P2.50mm_Vertical
J4: Conn_02x05_Odd_Even; IDC-Header_2x05_P2.54mm_Vertical
J5: LoLi_1; JST_XA_B05B-XASK-1_1x05_P2.50mm_Vertical
J6: LoLi_2; JST_XA_B05B-XASK-1_1x05_P2.50mm_Vertical
J7: Conn_01x02_Pin; AMASS_XT60PW-M_1x02_P7.20mm_Horizontal
J8, J9: Conn_01x02_Pin; AMASS_XT60-F_1x02_P7.20mm_Vertical
J10: USB_C_Receptacle_USB2.0_16P; USB_C_Receptacle_HRO_TYPE-C-31-M-12
J11: Steering_pin; PinSocket_2x04_P2.54mm_Vertical
J12: Drive_pin; PinSocket_2x04_P2.54mm_Vertical
LED1, LED2: SMLVN6RGB; LED_ROHM_SMLVN6
R1: 10k; R_0603_1608Metric_Pad0.98x0.95mm_HandSolder
R2, R3: 0.5m; R_2512_6332Metric
R4, R8, R9, R10, R11, R12, R13: 1k; R_0603_1608Metric_Pad0.98x0.95mm_HandSolder
R5, R6: 5.1k; R_0603_1608Metric_Pad0.98x0.95mm_HandSolder
R7: 120; R_0603_1608Metric_Pad0.98x0.95mm_HandSolder
SW1: RESET; SW_PUSH_6mm
SW2: SW_DIP_x08; DIP-16_W7.62mm
U1: STM32F405RGTx; LQFP-64_10x10mm_P0.5mm
U2, U3: NCS214; SOT-363_SC-70-6_Handsoldering
U4: Regulator_5.0; TO-252-2
U5: Regulator_3.3; TO-252-2
U6: NJM7812; TO-252-2
U7: CH340E; MSOP-10_3x3mm_P0.5mm
U8: MCP2561-E-SN; SOIC-8_3.9x4.9mm_P1.27mm
Y1: 16MHz; Crystal_HC18-U_Vertical

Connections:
+3.3V: C14.1, C15.1, C16.1, C17.1, C20.1, C21.1, C22.1, FB1.2, J4.7, J4.8, J5.2, J6.2, U1.1 (VBAT), U1.16 (PA2), U1.19 (VDD), U1.32 (VDD), U1.48 (VDD), U1.64 (VDD), U2.3 (Vs), U3.3 (Vs), U5.3 (VO)
+5V: C9.1, C10.1, J4.9, J4.10, J13.A4 (VBUS), J13.A9 (VBUS__1), J13.B4 (VBUS__2), J13.B9 (VBUS__3), U4.3 (VO), U8.3 (VDD)
+12V: C8.1, C11.1, C12.1, C13.1, U4.1 (VI), U5.1 (VI), U6.3 (VO)
+24V: C6.1, C7.1, J7.2, R2.1, R3.1, U2.4 (+IN), U3.4 (+IN), U6.1 (VI)
CAN_H: J1.A6 (DP1), J1.B6 (DP2), J13.A6 (DP1), J13.B6 (DP2), SW2.8, U8.7 (CANH)
CAN_L: J1.A7 (DN1), J1.B7 (DN2), J13.A7 (DN1), J13.B7 (DN2), R7.2, U8.6 (CANL)
CAN_RX: U1.44 (PA11), U8.4 (RXD)
CAN_TX: U1.45 (PA12), U8.1 (TXD)
DIP_SW_1: SW2.1, U1.24 (PC4)
DIP_SW_2: SW2.2, U1.25 (PC5)
DIP_SW_3: SW2.3, U1.26 (PB0)
DIP_SW_4: SW2.4, U1.27 (PB1)
DIP_SW_5: SW2.5, U1.28 (PB2)
DIP_SW_6: SW2.6, U1.29 (PB10)
DIP_SW_7: SW2.7, U1.30 (PB11)
Drive_ADC: U1.21 (PA5), U3.6 (OUT)
Drive_PWM_A: J12.6, J12.8, U1.59 (PB7)
Drive_PWM_B: J12.2, J12.4, U1.58 (PB6)
ENCODER_1_A: J5.3, U1.42 (PA9)
ENCODER_1_B: J5.1, U1.41 (PA8)
ENCODER_2_A: J6.3, U1.14 (PA0)
ENCODER_2_B: J6.1, U1.15 (PA1)
GND: C1.2, C2.2, C3.2, C4.2, C5.2, C6.2, C7.2, C8.2, C9.2, C10.2, C11.2, C12.2, C13.2, C14.2, C15.2, C16.2, C17.2, C18.2, C19.2, C20.2, C21.2, C22.2, J2.2, J3.2, J4.5, J4.6, J5.5, J6.5, J7.1, J8.1, J9.1, J10.A1 (GND), J10.A12 (GND), J10.B1 (GND), J10.B12 (GND), J10.S1 (SHIELD), J11.1, J11.3, J11.5, J11.7, J12.1, J12.3, J12.5, J12.7, J13.A1 (GND), J13.A12 (GND__1), J13.B1 (GND__2), J13.B12 (GND__3), J13.SH1 (SHIELD), J13.SH2 (SHIELD__1), J13.SH3 (SHIELD__2), J13.SH4 (SHIELD__3), LED1.4 (GK), LED1.5 (RK), LED1.6 (BK), LED2.4 (GK), LED2.5 (RK), LED2.6 (BK), R1.1, R4.1, R5.2, R6.1, SW1.1, SW2.10, SW2.11, SW2.12, SW2.13, SW2.14, SW2.15, SW2.16, U1.12 (VSSA), U1.17 (PA3), U1.18 (VSS), U1.63 (VSS), U2.1 (REF), U2.2 (GND), U3.1 (REF), U3.2 (GND), U4.2 (GND), U5.2 (GND), U6.2 (GND), U7.3 (GND), U8.2 (VSS), U8.8 (STBY)
LED1_B: R8.2, U1.8 (PC0)
LED1_G: R10.2, U1.10 (PC2)
LED1_R: R9.2, U1.9 (PC1)
LED2_B: R11.2, U1.2 (PC13)
LED2_G: R13.2, U1.4 (PC15)
LED2_R: R12.2, U1.3 (PC14)
Limit_SW_Left: J2.1, U1.39 (PC8)
Limit_SW_Right: J3.1, U1.38 (PC7)
NRST: C1.1, J4.1, SW1.2, U1.7 (NRST)
unnamed: J8.2, R2.2, U2.5 (-IN)
unnamed: J9.2, R3.2, U3.5 (-IN)
unnamed: J10.A5 (CC1), R5.1
unnamed: J10.B5 (CC2), R6.2
unnamed: LED1.1 (BA), R8.1
unnamed: LED1.3 (GA), R10.1
unnamed: LED1.2 (RA), R9.1
unnamed: LED2.1 (BA), R11.1
unnamed: LED2.3 (GA), R13.1
unnamed: LED2.2 (RA), R12.1
unnamed: R7.1, SW2.9
unnamed: R1.2, U1.60 (BOOT0)
unnamed: C3.1, U1.5 (PH0), Y1.2
unnamed: C2.1, U1.6 (PH1), Y1.1
unnamed: C5.1, U1.31 (VCAP_1)
unnamed: C4.1, U1.47 (VCAP_2)
unnamed: FB1.1, U1.13 (VDDA)
unnamed: R4.2, U7.6 (TNOW)
unnamed: J10.A6 (D+), J10.B6 (D+), U7.1 (UD+)
unnamed: J10.A7 (D-), J10.B7 (D-), U7.2 (UD-)
unnamed: C18.1, U7.10 (V3)
unnamed: C19.1, J10.A4 (VBUS), J10.A9 (VBUS), J10.B4 (VBUS), J10.B9 (VBUS), U7.7 (VCC)
SWCLK: J4.2, U1.49 (PA14)
SWDIO: J4.4, U1.46 (PA13)
Steering_ADC: U1.20 (PA4), U2.6 (OUT)
Steering_PWM_A: J11.6, J11.8, U1.22 (PA6)
Steering_PWM_B: J11.2, J11.4, U1.23 (PA7)
VCP_RX: U1.54 (PD2), U7.8 (TXD)
VCP_TX: U1.53 (PC12), U7.9 (RXD)

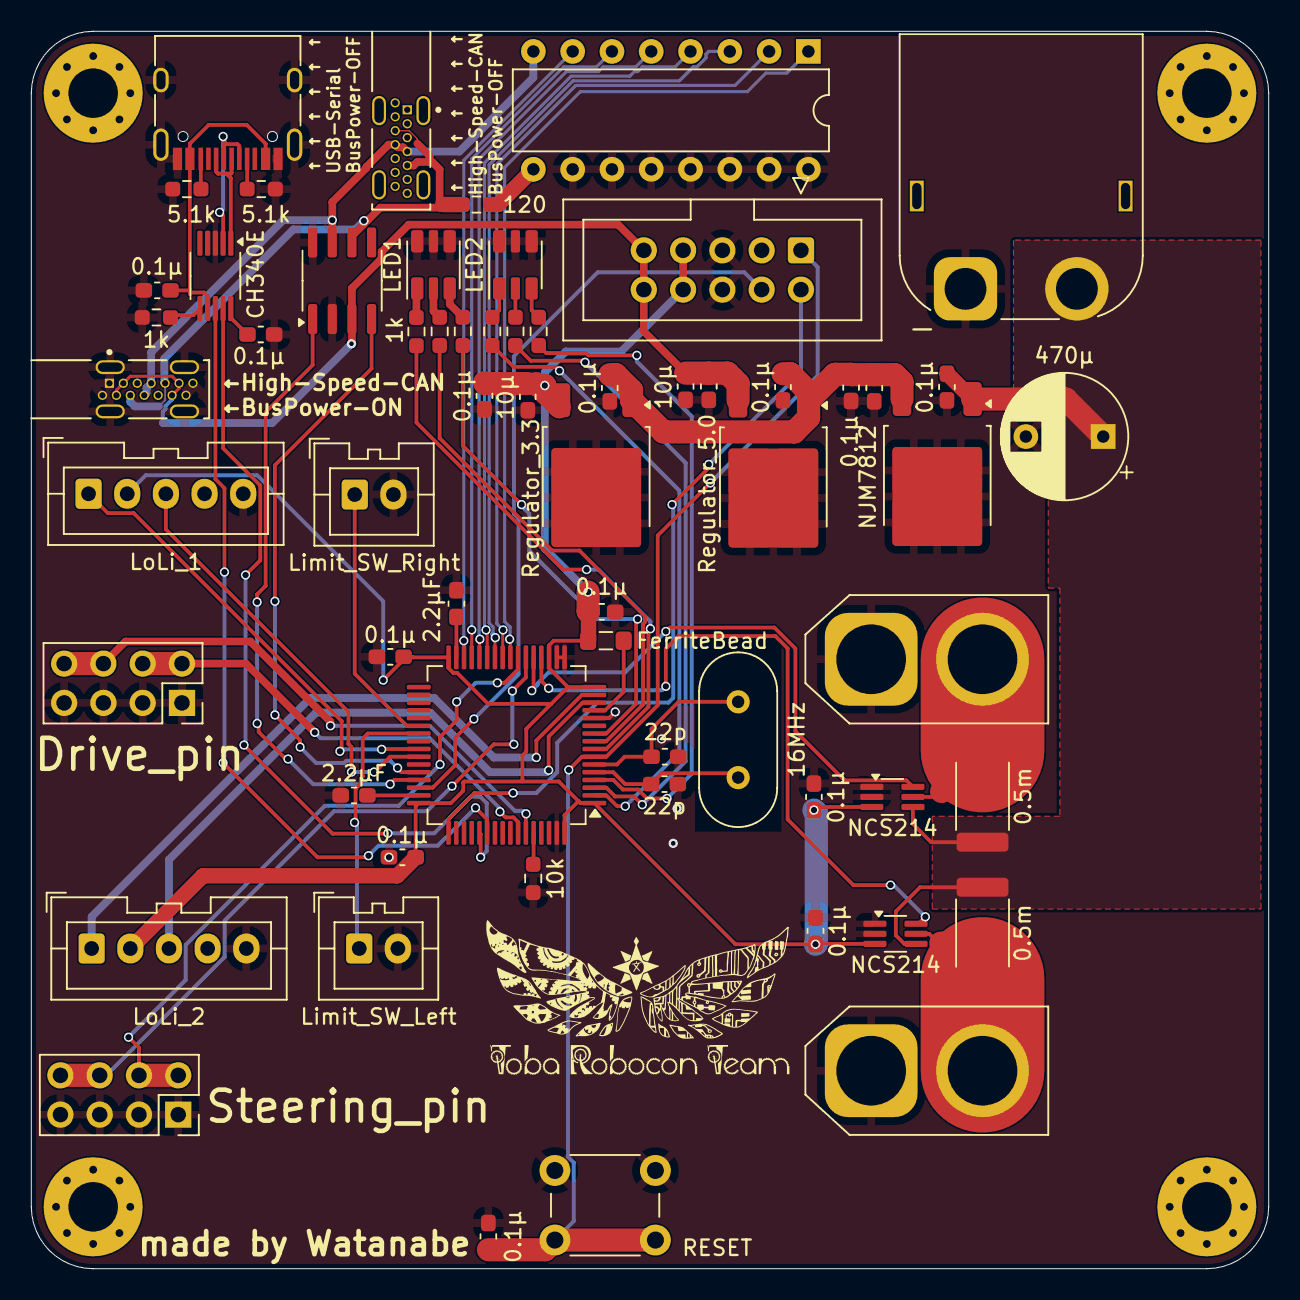
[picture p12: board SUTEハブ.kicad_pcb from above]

Board: 2 copper layers, 80.0 x 80.0 mm, 62 parts (0 on the bottom side), 61 nets.

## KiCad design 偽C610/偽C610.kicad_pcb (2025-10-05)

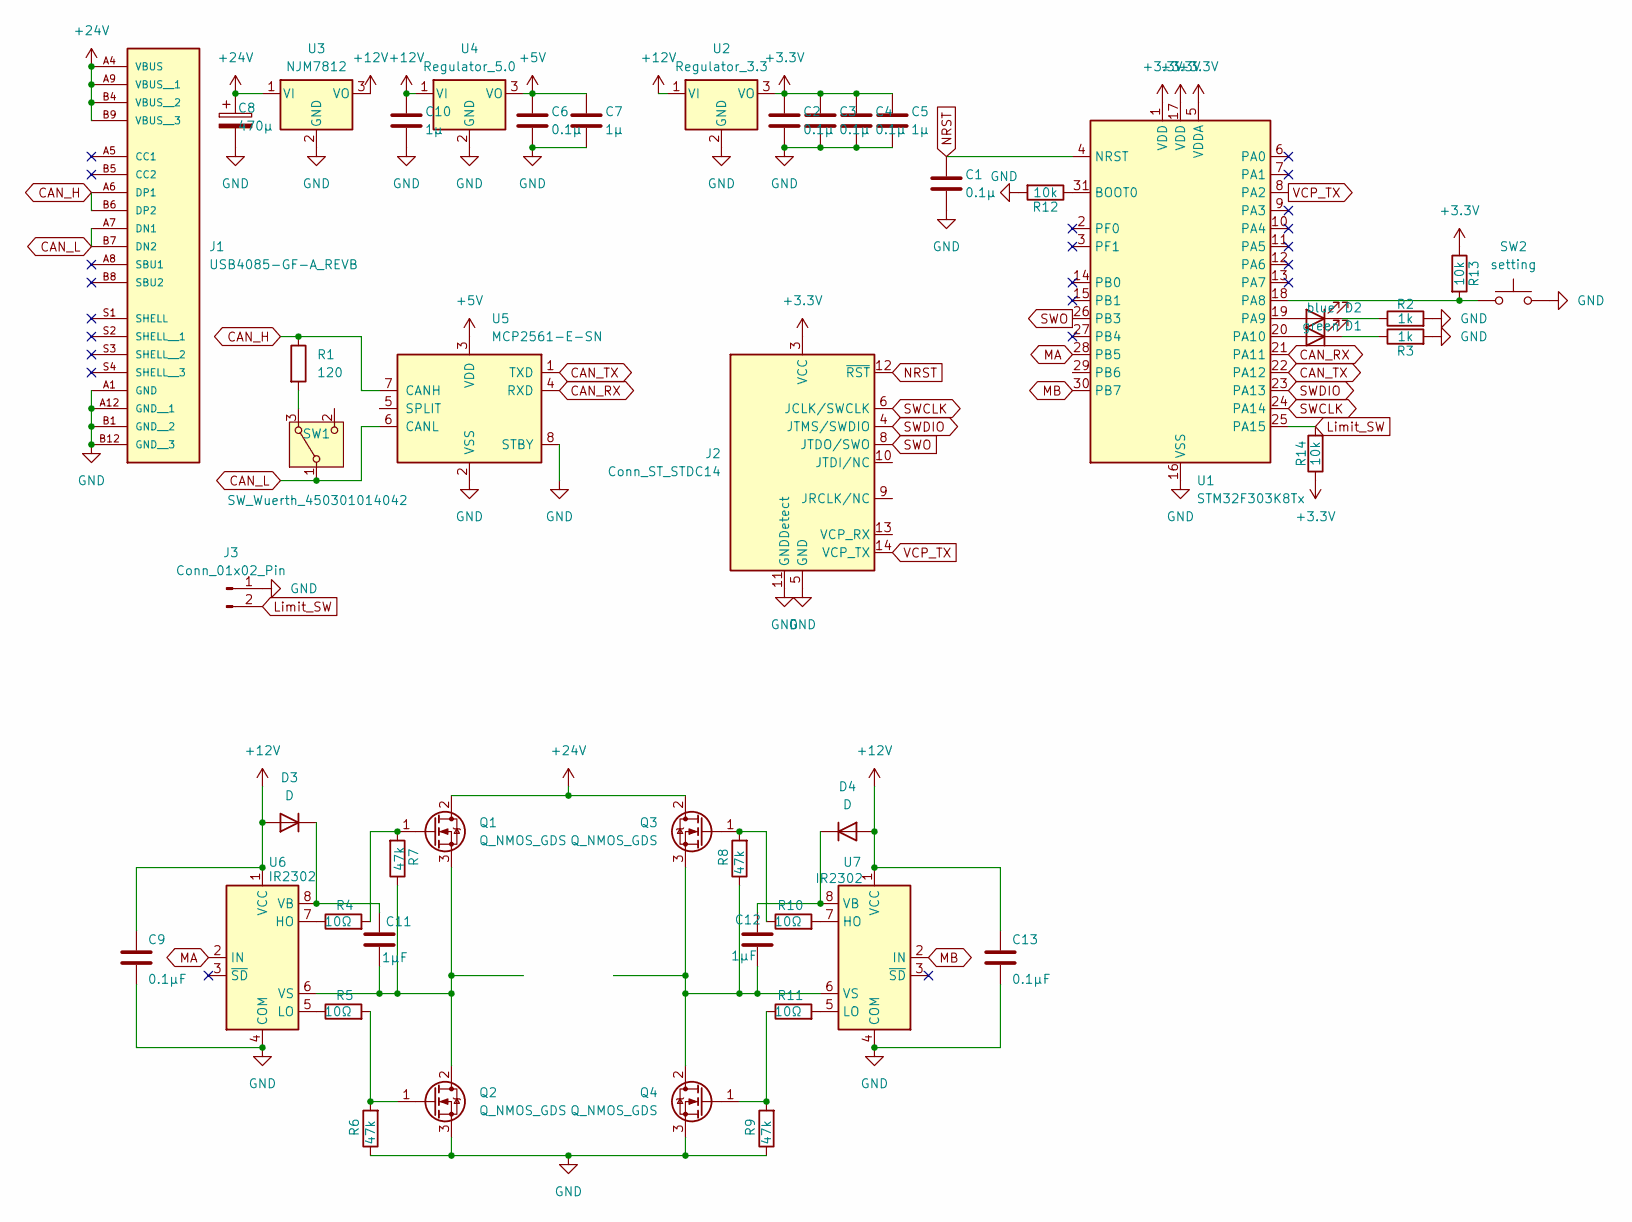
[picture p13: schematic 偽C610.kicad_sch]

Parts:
C1, C2, C3, C4, C6: 0.1μ; C_0603_1608Metric
C5, C7, C10: 1μ; C_0603_1608Metric
C8: 470μ; CP_Radial_D8.0mm_P3.50mm
C9, C13: 0.1μF; C_0603_1608Metric_Pad1.08x0.95mm_HandSolder
C11, C12: 1μF; C_0603_1608Metric_Pad1.08x0.95mm_HandSolder
D1: green; LED_0603_1608Metric
D2: blue; LED_0603_1608Metric
D3, D4: D; D_SOD-123F
J1: USB4085-GF-A_REVB; GCT_USB4085-GF-A_REVB; PARTREV B
J2: Conn_ST_STDC14; PinHeader_2x07_P1.27mm_Vertical
J3: Conn_01x02_Pin; JST_PH_B2B-PH-SM4-TB_1x02-1MP_P2.00mm_Vertical
Q1, Q2, Q3, Q4: Q_NMOS_GDS; TO-252-2
R1: 120; R_0603_1608Metric
R2, R3: 1k; R_0603_1608Metric
R4, R5, R10, R11: 10Ω; R_0603_1608Metric_Pad0.98x0.95mm_HandSolder
R6, R7, R8, R9: 47k; R_0603_1608Metric_Pad0.98x0.95mm_HandSolder
R12, R13, R14: 10k; R_0603_1608Metric
SW1: SW_Wuerth_450301014042; SW_Slide-03_Wuerth-WS-SLTV_10x2.5x6.4_P2.54mm
SW2: setting; SW_PUSH_1P1T_6x3.5mm_H5.0_APEM_MJTP1250
U1: STM32F303K8Tx; LQFP-32_7x7mm_P0.8mm
U2: Regulator_3.3; TO-252-2
U3: NJM7812; TO-252-2
U4: Regulator_5.0; TO-252-2
U5: MCP2561-E-SN; SOIC-8_3.9x4.9mm_P1.27mm
U6, U7: IR2302; SOIC-8_3.9x4.9mm_P1.27mm

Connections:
+3.3V: C2.1, C3.1, C4.1, C5.1, J2.3 (VCC), R13.1, R14.1, U1.1 (VDD), U1.5 (VDDA), U1.17 (VDD), U2.3 (VO)
+5V: C6.1, C7.1, U4.3 (VO), U5.3 (VDD)
+12V: C9.1, C10.1, C13.1, D3.2 (A), D4.2 (A), U2.1 (VI), U3.3 (VO), U4.1 (VI), U6.1 (VCC), U7.1 (VCC)
+24V: C8.1, J1.A4 (VBUS), J1.A9 (VBUS__1), J1.B4 (VBUS__2), J1.B9 (VBUS__3), Q1.2 (D), Q3.2 (D), U3.1 (VI)
CAN_H: J1.A6 (DP1), J1.B6 (DP2), R1.1, U5.7 (CANH)
CAN_L: J1.A7 (DN1), J1.B7 (DN2), SW1.1 (B), U5.6 (CANL)
CAN_RX: U1.21 (PA11), U5.4 (RXD)
CAN_TX: U1.22 (PA12), U5.1 (TXD)
GND: C1.2, C2.2, C3.2, C4.2, C5.2, C6.2, C7.2, C8.2, C9.2, C10.2, C13.2, J1.A1 (GND), J1.A12 (GND__1), J1.B1 (GND__2), J1.B12 (GND__3), J2.5 (GND), J2.7 (GND), J2.11 (GNDDetect), J3.1, Q2.3 (S), Q4.3 (S), R2.2, R3.2, R6.1, R9.1, R12.2, SW2.2, U1.16 (VSS), U1.32 (VSS), U2.2 (GND), U3.2 (GND), U4.2 (GND), U5.2 (VSS), U5.8 (STBY), U6.4 (COM), U7.4 (COM)
Limit_SW: J3.2, R14.2, U1.25 (PA15)
MA: U1.28 (PB5), U6.2 (IN)
MB: U1.30 (PB7), U7.2 (IN)
NRST: C1.1, J2.12 (~RST), U1.4 (NRST)
unnamed: D1.2 (A), U1.20 (PA10)
unnamed: D1.1 (K), R3.1
unnamed: D2.2 (A), U1.19 (PA9)
unnamed: D2.1 (K), R2.1
unnamed: C11.1, D3.1 (K), U6.8 (VB)
unnamed: C12.1, D4.1 (K), U7.8 (VB)
unnamed: Q1.1 (G), R4.2, R7.2
unnamed: C11.2, Q1.3 (S), Q2.2 (D), R7.1, U6.6 (VS)
unnamed: Q2.1 (G), R5.2, R6.2
unnamed: Q3.1 (G), R8.2, R10.1
unnamed: C12.2, Q3.3 (S), Q4.2 (D), R8.1, U7.6 (VS)
unnamed: Q4.1 (G), R9.2, R11.1
unnamed: R1.2, SW1.3 (A)
unnamed: R12.1, U1.31 (BOOT0)
unnamed: R13.2, SW2.1, U1.18 (PA8)
unnamed: R4.1, U6.7 (HO)
unnamed: R5.1, U6.5 (LO)
unnamed: R10.2, U7.7 (HO)
unnamed: R11.2, U7.5 (LO)
SWCLK: J2.6 (JCLK/SWCLK), U1.24 (PA14)
SWDIO: J2.4 (JTMS/SWDIO), U1.23 (PA13)
SWO: J2.8 (JTDO/SWO), U1.26 (PB3)
VCP_TX: J2.14 (VCP_TX), U1.8 (PA2)

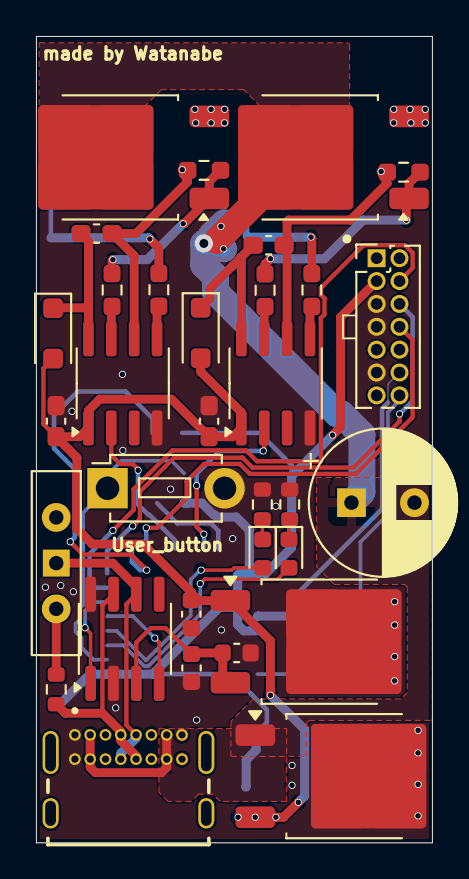
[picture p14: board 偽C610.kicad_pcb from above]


Board: 2 copper layers, 22.0 x 44.8 mm, 47 parts (15 on the bottom side), 36 nets.

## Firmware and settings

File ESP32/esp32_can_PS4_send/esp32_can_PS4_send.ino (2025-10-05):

#include "CAN.h"
#include "PS4Controller.h"

void setup() {
  if(!CAN.begin(1000E3)) //通信速度
  {
    while (1);
    //送信不可
  }
  volatile uint32_t* pREG_IER = (volatile uint32_t*)0x3ff6b010;
  *pREG_IER &= ~(uint8_t)0x10;

  PS4.begin(""); //←ESP32のBluetoothMACアドレスをぶち込んで
}

void loop() {
  CAN.beginPacket(0x00);//パケット1送信開始
  
  CAN.write(0x01);//ヘッダー1

  //LスティックYの送信
  if(PS4.LStickY() >= 0){
    CAN.write(PS4.LStickY());
  }
  else{
    CAN.write(0);
  }
  if(PS4.LStickY() <= 0){
    CAN.write(-PS4.LStickY());
  }
  else{
    CAN.write(0);
  }
  //LスティックYの送信ここまで

  //LスティックXの送信
  if(PS4.LStickX() >= 0){
    CAN.write(PS4.LStickX());
  }
  else{
    CAN.write(0);
  }
  if(PS4.LStickX() <= 0){
    CAN.write(-PS4.LStickX());
  }
  else{
    CAN.write(0);
  }
  //LスティックXの送信ここまで

  //RスティックYの送信
  if(PS4.RStickY() >= 0){
    CAN.write(PS4.RStickY());
  }
  else{
    CAN.write(0);
  }
  if(PS4.RStickY() <= 0){
    CAN.write(-PS4.RStickY());
  }
  else{
    CAN.write(0);
  }
  //RスティックYの送信ここまで

  //RスティックXの送信
  if(PS4.RStickX() >= 0){
    CAN.write(PS4.RStickX());
  }
  else{
    CAN.write(0);
  }
  CAN.endPacket();//パケット1送信完了

  CAN.beginPacket(0x00);//パケット2送信開始
  
  CAN.write(0x02);//ヘッダー2

  if(PS4.RStickX() <= 0){
    CAN.write(-PS4.RStickX());
  }
  else{
    CAN.write(0);
  }
  //RスティックXの送信ここまで

  CAN.write(PS4.Up());//十字↑
  CAN.write(PS4.Right());//十字→
  CAN.write(PS4.Down());//十字↓
  CAN.write(PS4.Left());//十字←
  CAN.write(PS4.Circle());//◯ボタン
  CAN.write(PS4.Cross());//☓ボタン

  CAN.endPacket();//パケット2送信完了

  CAN.beginPacket(0x00);//パケット3送信開始
  
  CAN.write(0x03);//ヘッダー3

  CAN.write(PS4.Triangle());//△ボタン
  CAN.write(PS4.Square());//□ボタン
  CAN.write(PS4.R1());//R1ボタン
  CAN.write(PS4.L1());//L1ボタン
  CAN.write(PS4.R2Value());//R2押し込み
  CAN.write(PS4.L2Value());//L2押し込み
  CAN.write(0x00);//偽物

  CAN.endPacket();//パケット3送信完了

  delay(30);

}

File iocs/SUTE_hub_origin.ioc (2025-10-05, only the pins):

Mcu.UserName=STM32F405RGTx
PA0-WKUP.GPIO_Label=ENCODER_2_A
PA0-WKUP.Signal=S_TIM2_CH1_ETR
PA1.GPIO_Label=ENCODER_2_B
PA1.Signal=S_TIM2_CH2
PA11.Signal=CAN1_RX
PA12.Signal=CAN1_TX
PA13.Signal=SYS_JTMS-SWDIO
PA14.Signal=SYS_JTCK-SWCLK
PA2.GPIO_Label=Vdd_ADC
PA2.Signal=ADCx_IN2
PA3.GPIO_Label=GND_ADC
PA3.Signal=ADCx_IN3
PA4.GPIO_Label=Steering_current
PA4.Signal=ADCx_IN4
PA5.GPIO_Label=Drive_current
PA5.Signal=ADCx_IN5
PA6.GPIO_Label=Steering_A
PA6.Signal=S_TIM3_CH1
PA7.GPIO_Label=Steering_B
PA7.Signal=S_TIM3_CH2
PA8.GPIO_Label=ENCODER_1_B
PA8.Signal=S_TIM1_CH1
PA9.GPIO_Label=ENCODER_1_A
PA9.Signal=S_TIM1_CH2
PB0.GPIO_Label=DIP_SW_3
PB0.Signal=GPIO_Input
PB1.GPIO_Label=DIP_SW_4
PB1.Signal=GPIO_Input
PB10.GPIO_Label=DIP_SW_6
PB10.Signal=GPIO_Input
PB11.GPIO_Label=DIP_SW_7
PB11.Signal=GPIO_Input
PB2.GPIO_Label=DIP_SW_5
PB2.Signal=GPXTI2
PB6.GPIO_Label=Drive_B
PB6.Signal=S_TIM4_CH1
PB7.GPIO_Label=Drive_A
PB7.Signal=S_TIM4_CH2
PC0.GPIO_Label=LED1_B
PC0.Signal=GPIO_Output
PC1.GPIO_Label=LED1_R
PC1.Signal=GPIO_Output
PC12.Signal=UART5_TX
PC13-ANTI_TAMP.GPIO_Label=LED2_B
PC13-ANTI_TAMP.Signal=GPIO_Output
PC14-OSC32_IN.GPIO_Label=LED2_R
PC14-OSC32_IN.Signal=GPIO_Output
PC15-OSC32_OUT.GPIO_Label=LED2_G
PC15-OSC32_OUT.Signal=GPIO_Output
PC2.GPIO_Label=LED1_G
PC2.Signal=GPIO_Output
PC4.GPIO_Label=DIP_SW_1
PC4.Signal=GPIO_Input
PC5.GPIO_Label=DIP_SW_2
PC5.Signal=GPIO_Input
PC7.GPIO_Label=Limit_SW_Right
PC7.Signal=GPXTI7
PC8.GPIO_Label=Limit_SW_Left
PC8.Signal=GPXTI8
PD2.Signal=UART5_RX
PH0-OSC_IN.Signal=RCC_OSC_IN
PH1-OSC_OUT.Signal=RCC_OSC_OUT

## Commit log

2025-10-05 GOD_DC_MDを追加
    [GOD_DC_MD.kicad_pcb, GOD_DC_MD.kicad_sch, GOD_DC_MD.step]
2025-10-05 iocファイルを追加
2025-10-05 ESP32でDualshock4の値を取得するプログラムを追加
2025-10-05 Dualshock4の値の規格表を追加
